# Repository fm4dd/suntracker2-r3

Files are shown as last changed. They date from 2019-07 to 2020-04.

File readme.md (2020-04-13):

# SunTracker2 Revision 3



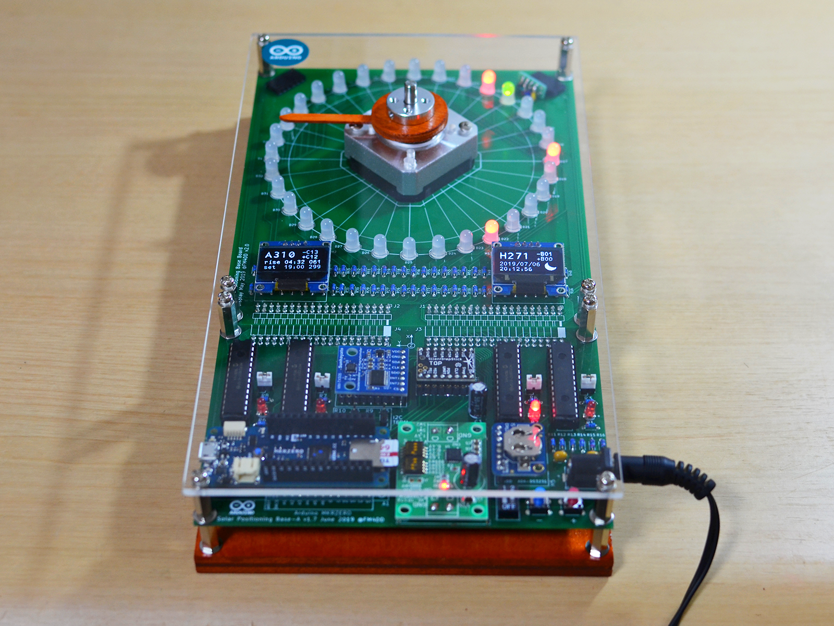
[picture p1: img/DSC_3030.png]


This project develops a photovoltaic (PV) solar tracking controller.
Pictured above is the current prototype. PV solar trackers control the PV
panel direction to keep the panel perpendicular to the Sun, maximizing the
power output. The power output difference for a fully aligned panel is
reported to be in a range of 15\~40%, which would be substantial.

## Design

The goal is a self-orienting dual-axis, scheduled, Arduino-based solar
tracker. I want to control PV panel orientation for both Elevation and
Azimuth angles (dual-axis), based on the calculated solar position of a PV
systems specific geographic location and time (scheduled).

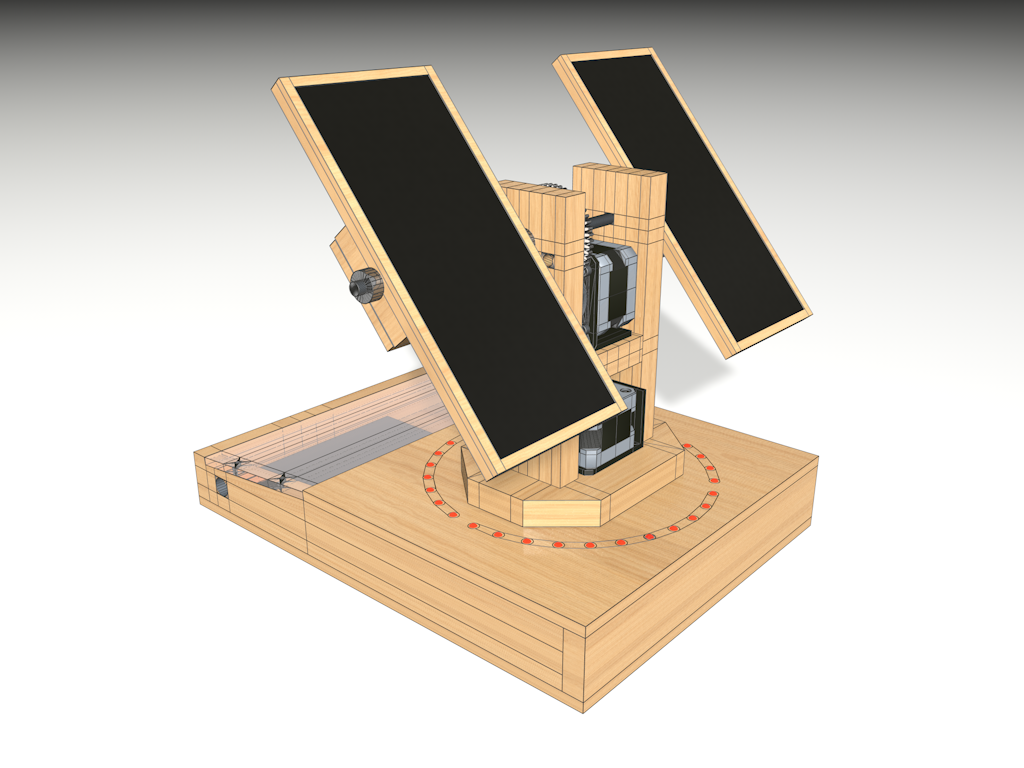
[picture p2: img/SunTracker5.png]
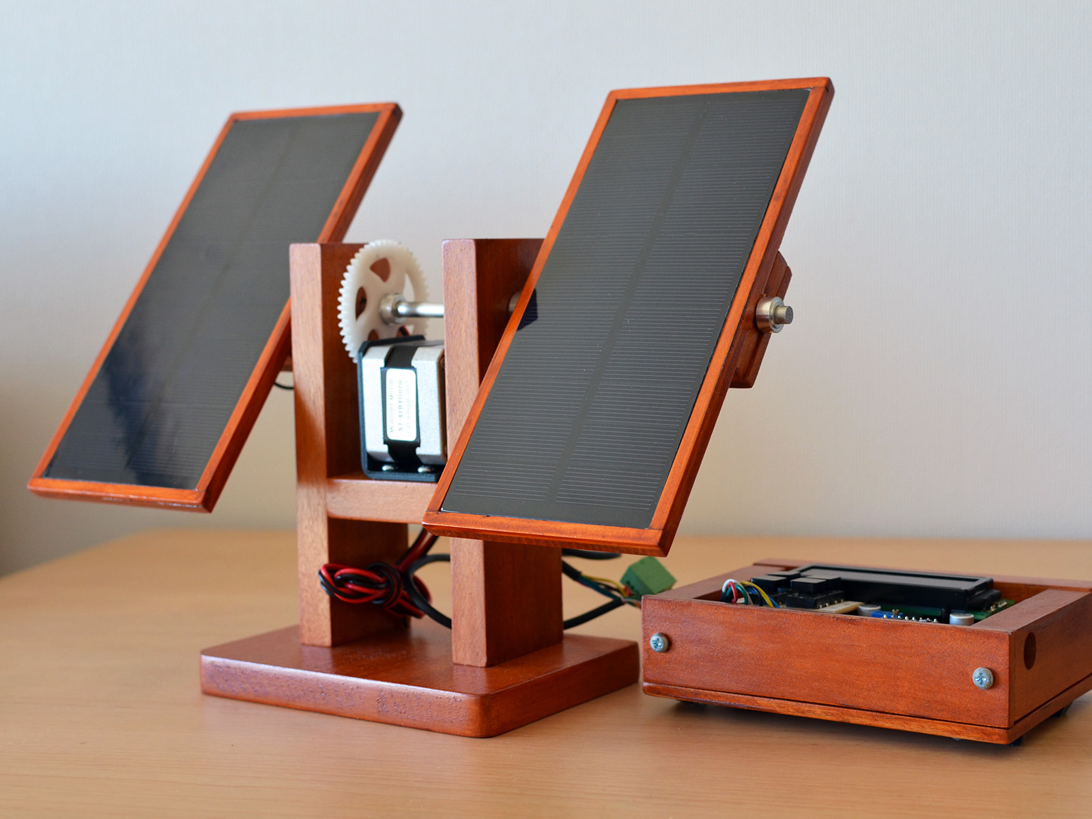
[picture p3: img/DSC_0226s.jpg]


Working under space, cost and time constraints, the prototype development is
done on a small scale model. Eventually, I want to control and optimize the
orientation of Mini-PV systems.

## Functional Design

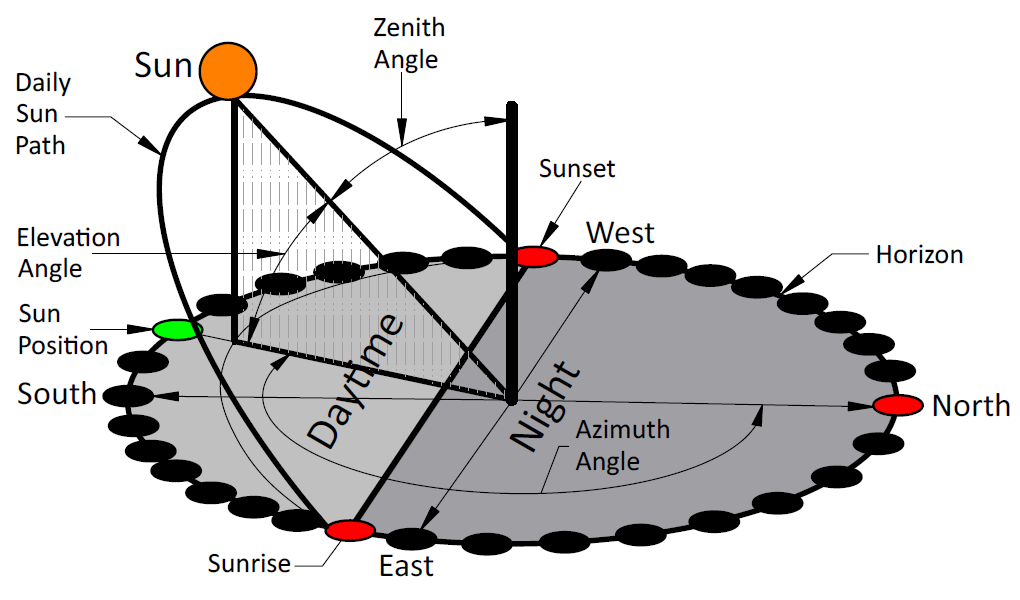
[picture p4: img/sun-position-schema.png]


In order to clearly understand and validate the sun tracking function, a 32
dual-color LED ring represents the horizon with north, sunrise and sunset
indicators. A green indicator displays the suns daily movement over time.
The optional NEMA stepper motor is used to develop the motor control code
for the solar panel horizontal alignment.

### Board Components

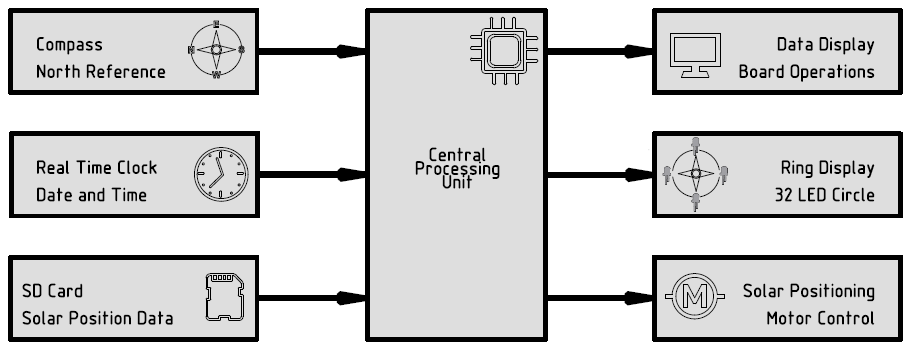
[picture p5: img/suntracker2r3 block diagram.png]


### Board Layout

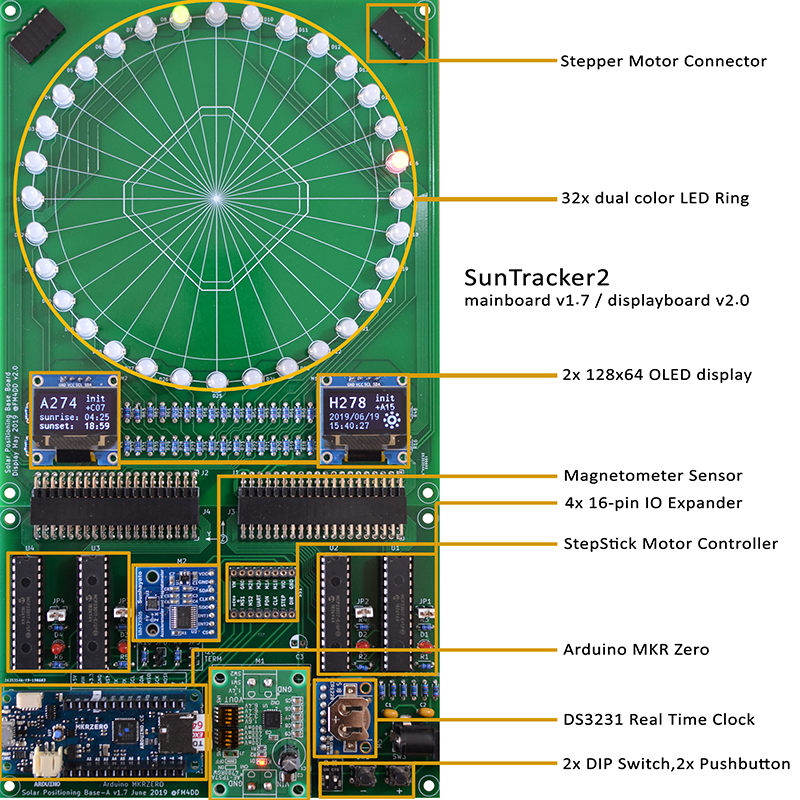
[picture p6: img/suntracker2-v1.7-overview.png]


The solar position data gets calculated off-system in advance, and saved into a
micro SD card. The pre-generated daily sun position files are then read by the
Arduino MKR Zero microcontroller through the onboard card reader. The
astronomical calculations of the suns position require sufficient CPU power, and
are taxing on Microcontrollers.

At the moment I am using a sun position dataset that covers two years of
operation, and uses approx. 20MB in size (46 MB with additional debug data). I
wrote the “suncalc” tool to pre-calculate the data set files for a specific
location, on a Linux PC.

### PCB

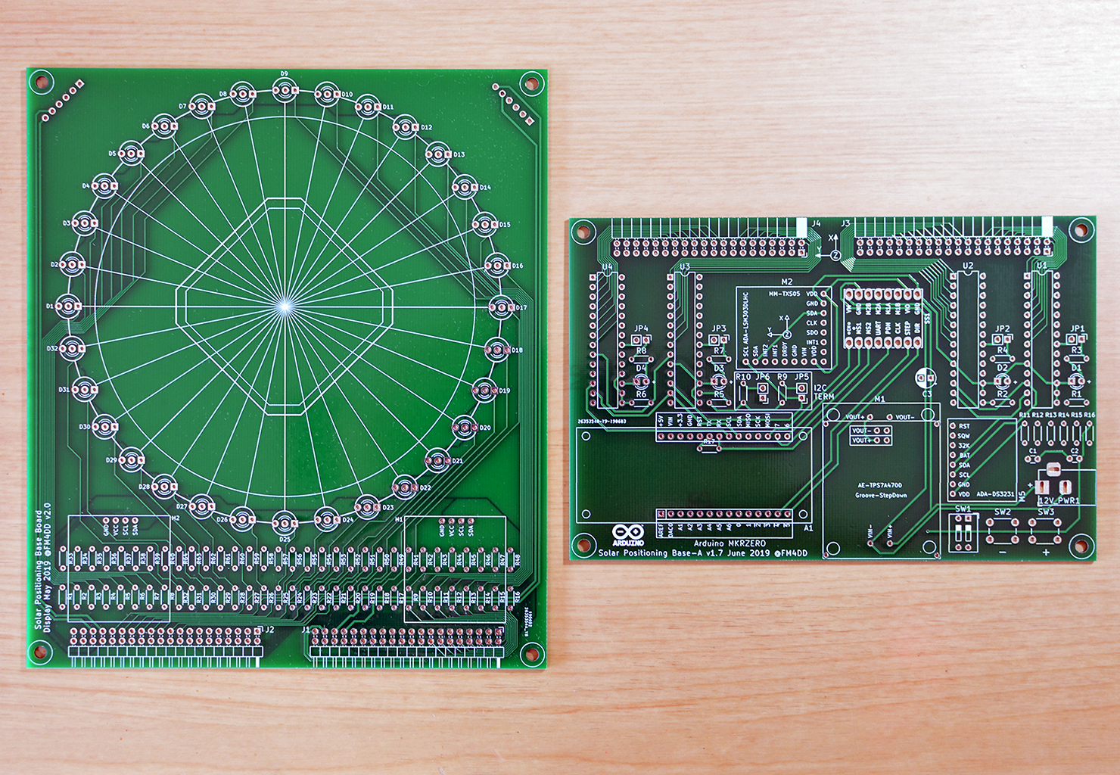
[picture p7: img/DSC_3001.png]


### Demo

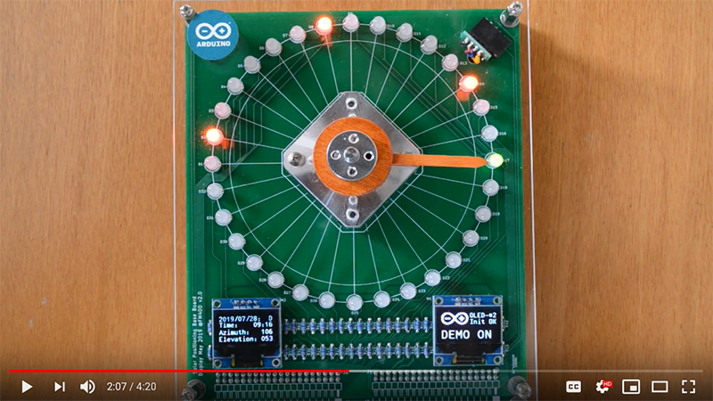
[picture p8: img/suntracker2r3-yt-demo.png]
Watch the video (https://youtu.be/e8dpviy-tlI)


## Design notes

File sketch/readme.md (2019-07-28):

# mainboard-rev3 sketch compilation

```
Sketch uses 64604 bytes (24%) of program storage space. Maximum is 262144 bytes.
Atmel SMART device 0x10010005 found
Device       : ATSAMD21G18A
Chip ID      : 10010005
Version      : v2.0 [Arduino:XYZ] Oct 20 2016 15:20:47
Address      : 8192
Pages        : 3968
Page Size    : 64 bytes
Total Size   : 248KB
Planes       : 1
Lock Regions : 16
Locked       : none
Security     : false
Boot Flash   : true
BOD          : true
BOR          : true
Arduino      : FAST_CHIP_ERASE
Arduino      : FAST_MULTI_PAGE_WRITE
Arduino      : CAN_CHECKSUM_MEMORY_BUFFER
Erase flash
done in 0.828 seconds

Write 65148 bytes to flash (1018 pages)

[=                             ] 6% (64/1018 pages)
[===                           ] 12% (128/1018 pages)
[=====                         ] 18% (192/1018 pages)
[=======                       ] 25% (256/1018 pages)
[=========                     ] 31% (320/1018 pages)
[===========                   ] 37% (384/1018 pages)
[=============                 ] 44% (448/1018 pages)
[===============               ] 50% (512/1018 pages)
[================              ] 56% (576/1018 pages)
[==================            ] 62% (640/1018 pages)
[====================          ] 69% (704/1018 pages)
[======================        ] 75% (768/1018 pages)
[========================      ] 81% (832/1018 pages)
[==========================    ] 88% (896/1018 pages)
[============================  ] 94% (960/1018 pages)
[==============================] 100% (1018/1018 pages)
done in 0.433 seconds

Verify 65148 bytes of flash with checksum.
Verify successful
done in 0.063 seconds
CPU reset.
```

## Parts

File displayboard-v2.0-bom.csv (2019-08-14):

Manufacturer Part Number | Manufacturer | Digi-Key Part Number | Customer Reference | Quantity | Description
RNMF14FTC330R | Stackpole Electronics Inc | S330CACT-ND | R1-32 | 32 | RES 330 OHM 1/4W 1% AXIAL
RNMF14FTC220R | Stackpole Electronics Inc | S220CACT-ND | R33-64 | 32 | RES 220 OHM 1/4W 1% AXIAL
PEC20DBAN | Sullins Connector Solutions | S2112E-20-ND | J1,J2 | 2 | CONN HEADER R/A 40POS 2.54MM
PPPC061LGBN-RC | Sullins Connector Solutions | S5481-ND | J3,J4 | 2 | CONN HDR 6POS 0.1 GOLD PCB R/A
ROB-09238 | SparkFun Electronics | 1568-1105-ND | M1 | 1 | STEPPER MOTOR HYBRID BIPOLAR 12V
LTL-30EHJ | Lite-On Inc. | 160-1057-ND | D1-32 | 32 | LED GRN/RED DIFFUSED T-1 3/4 T/H
SKU-0049 | SUNHOKEY Electronics Co Ltd | N/A | OLED1,OLED2 | 2 | 128X64 0.96 inch OLED Display Module SSD1306 chipset

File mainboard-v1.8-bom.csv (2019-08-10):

Manufacturer Part Number | Manufacturer | Digi-Key Part Number | Customer Reference | Quantity | Description
ABX00012 | Arduino | 1050-1137-ND | A1 | 1 | ARDUINO MKR ZERO W/ HDR ATSAMD21
MCP23017-E/SP | Microchip Technology | MCP23017-E/SP-ND | U1,U2,U3,U4 | 4 | IC I/O EXPANDER I2C 16B 28SDIP
ED281DT | On Shore Technology Inc. | ED3050-5-ND | SU1, SU2, SU3, SU4 | 4 | CONN IC DIP SOCKET 28POS TIN
1120 | Adafruit Industries LLC | 1528-1173-ND | M2 | 1 | BOARD ACCEL/COMPASS 3AXIS LSM303
3013 | Adafruit Industries LLC | 1528-1598-ND | M5 | 1 | ADAFRUIT DS3231 PRECISION RTC BR
TMC2208 SILENTSTEPSTICK | Trinamic Motion Control GmbH | 1460-1201-ND | SS1 | 1 | TMC2208 STEPPER DRIVER BOARD
1825057-1 | TE Connectivity ALCOSWITCH Switches | 450-1363-ND | SWI1 | 1 | SWITCH SLIDE DIP SPST 100MA 24V
151031SS04000 | Wurth Electronics Inc. | 732-5005-ND | D1,D2,D3,D4 | 4 | LED RED DIFFUSED 3MM ROUND T/H
C320C105K5N5TA91707301 | KEMET | 399-14394-1-ND | C1,C2 | 2 | CAP CER 1UF 50V X8L RADIAL
68786-102LF | Amphenol ICC (FCI) | 609-3121-ND | JP1,JP2,JP3,JP4,JP5,JP6 | 6 | CONN SHUNT 2POS .100 LOPRO GOLD
476CKE035M | Illinois Capacitor | 1572-1473-ND | C3 | 1 | CAP ALUM 47UF 20% 35V RADIAL
PPTC202LJBN-RC | Sullins Connector Solutions | S5534-ND | J3,J4 | 2 | CONN HDR 40POS 0.1 TIN PCB R/A
SMC-1-40-1-GT | Adam Tech | 2057-SMC-1-40-1-GT-ND | Circuit Sockets | 2 | MACHINE PIN SOCKET 40P 1.00MM PI
1825910-6 | TE Connectivity ALCOSWITCH Switches | 450-1650-ND | SWI2,SWI3 | 2 | SWITCH TACTILE SPST-NO 0.05A 24V
RNMF14FTC10K0 | Stackpole Electronics Inc | S10KCACT-ND | R1,R2,R5,R6,R9,R10,R11,R12,R13,R14 | 10 | RES 10K OHM 1/4W 1% AXIAL
RNMF14FTC330R | Stackpole Electronics Inc | S330CACT-ND | R3,R4,R7,R8 | 4 | RES 330 OHM 1/4W 1% AXIAL
RNMF14FTC2K20 | Stackpole Electronics Inc | S2.2KCACT-ND | R15,R16 | 2 | RES 2.2K OHM 1/4W 1% AXIAL
PJ-002A | CUI Inc. | CP-002A-ND | 12V Barrel Jack | 1 | CONN PWR JACK 2X5.5MM SOLDER

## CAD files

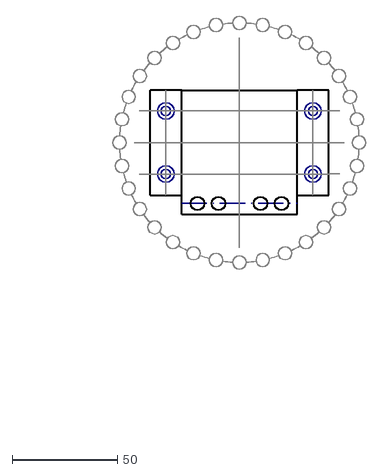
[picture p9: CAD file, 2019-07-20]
cad/32LED ring -114cm with Stand.dxf
166.4 x 198.3

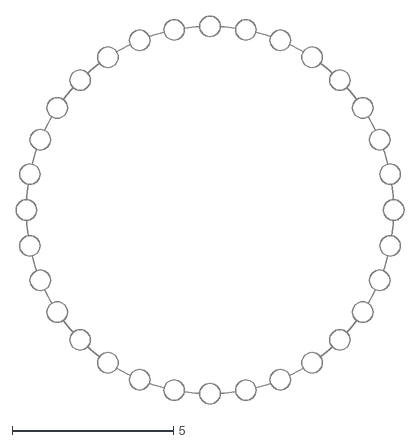
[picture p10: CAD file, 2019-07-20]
cad/32LED ring -114cm.dxf
12.0 x 12.0

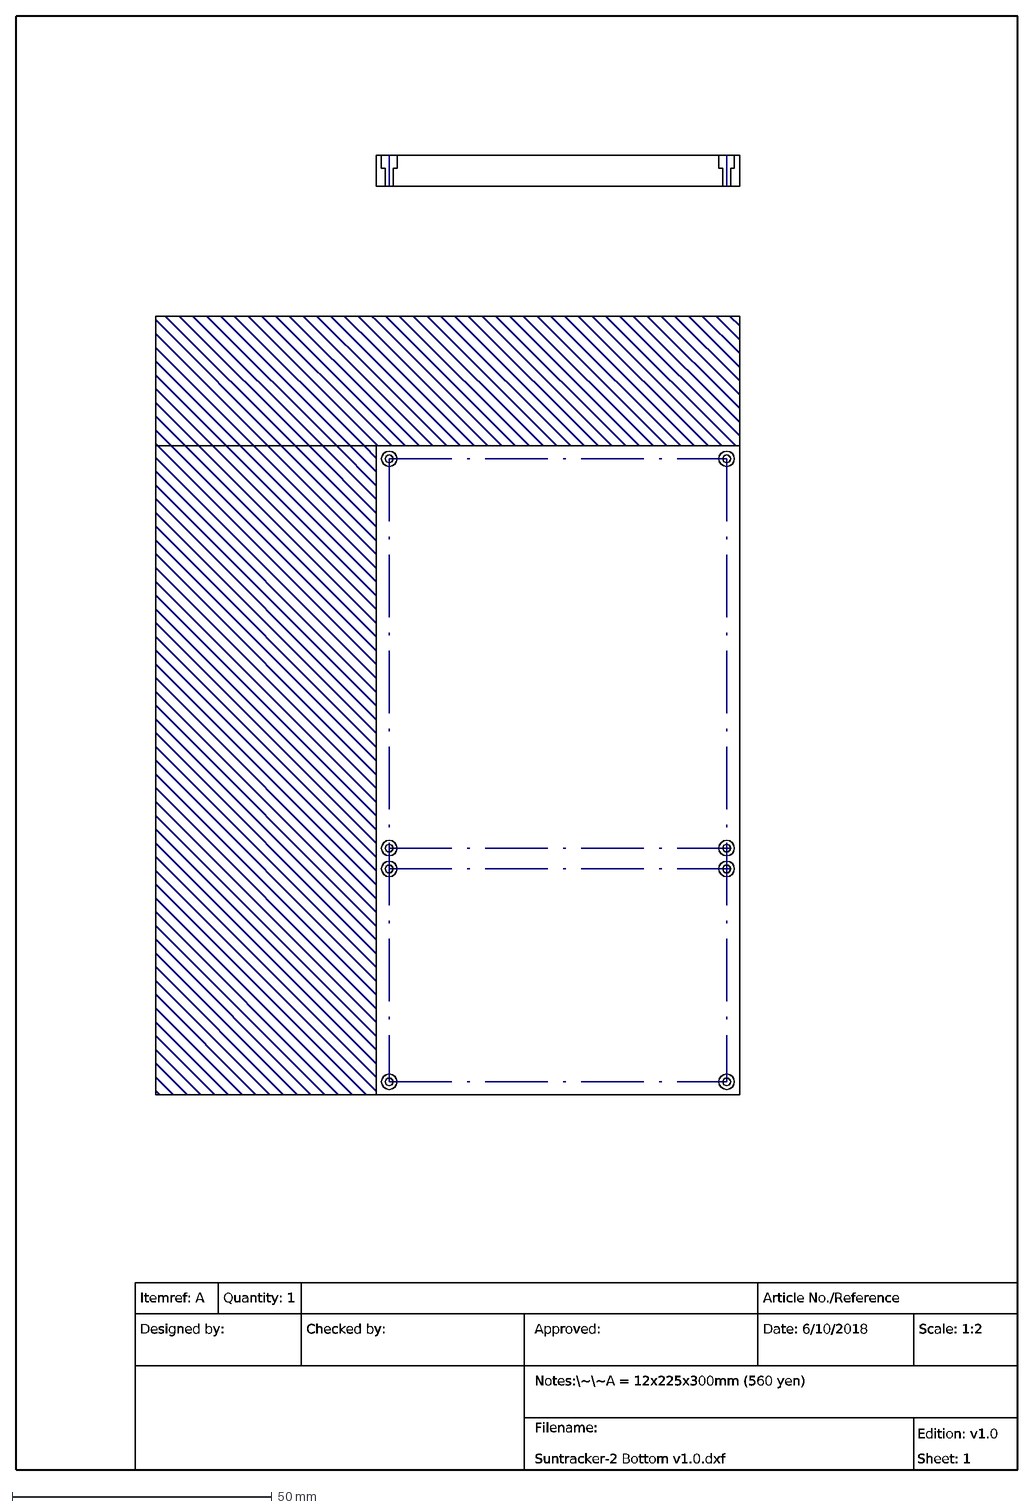
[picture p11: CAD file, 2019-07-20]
cad/20190620 Suntracker2 Bottom v1.0.dxf
Notes:\~\~A = 12x225x300mm (560 yen)
Itemref: A
Quantity: 1
Article No./Reference
Designed by:
Checked by:
Approved:
Filename: Suntracker-2 Bottom v1.0.dxf
Date: 6/10/2018
Scale: 1:2
Edition: v1.0 Sheet: 1

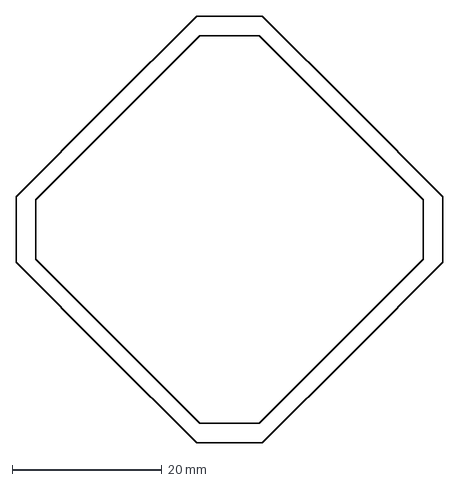
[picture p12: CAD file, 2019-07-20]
cad/20190601 stepper motor footprint.dxf
57.0 x 57.0 mm

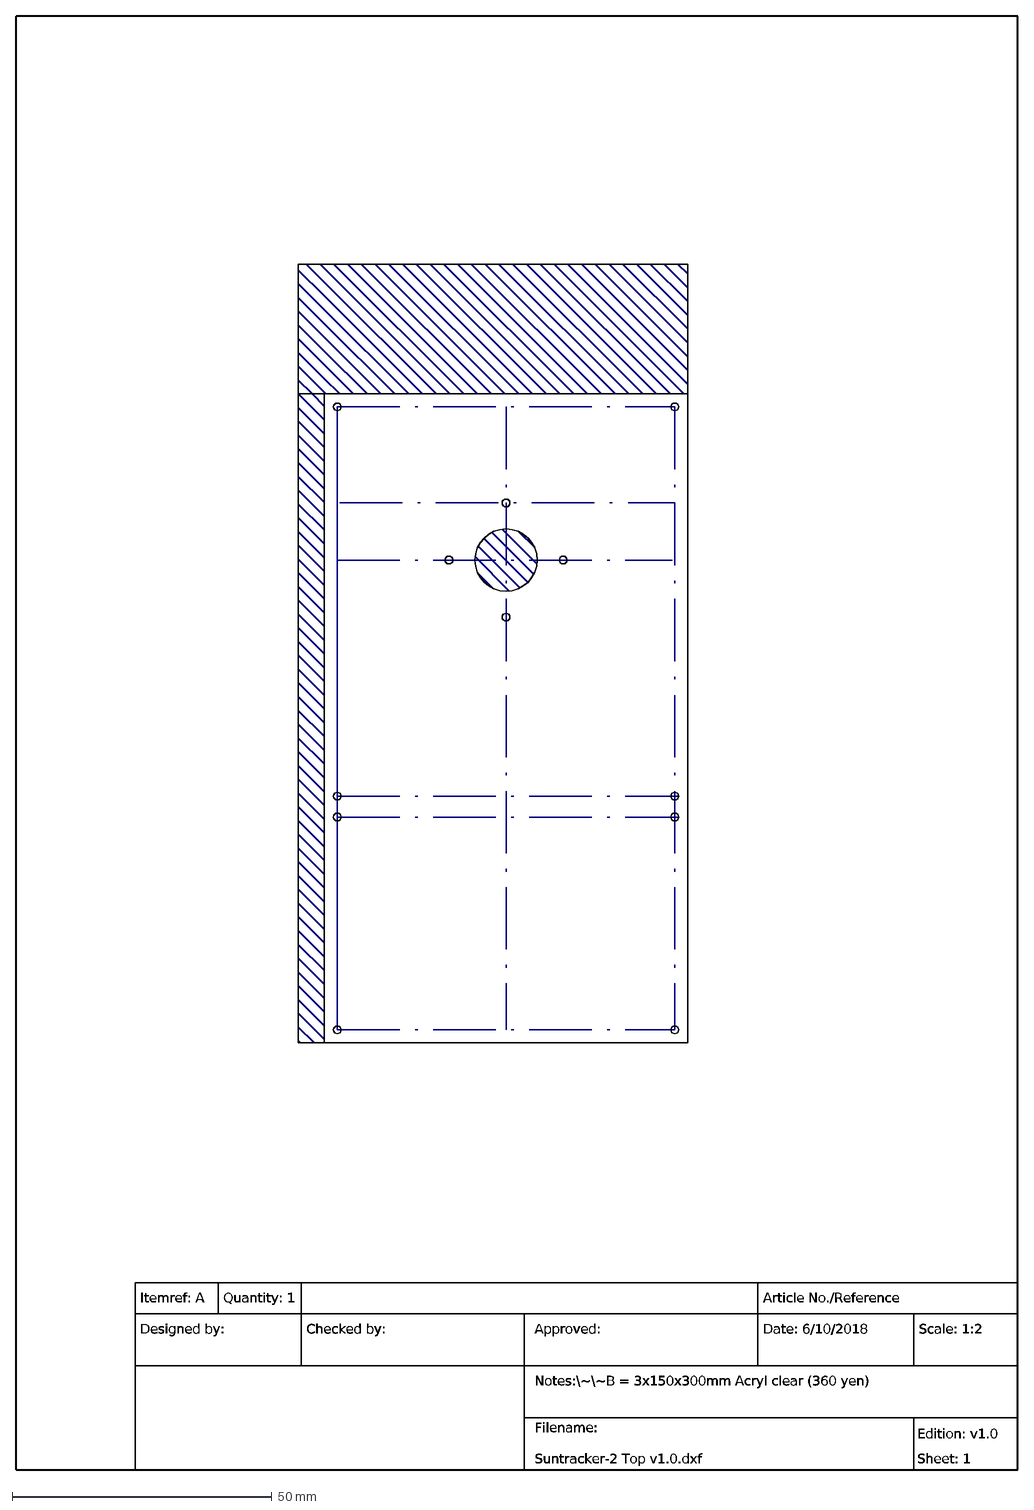
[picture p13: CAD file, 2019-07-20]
cad/20190620 Suntracker2 Top v1.0.dxf
Notes:\~\~B = 3x150x300mm Acryl clear (360 yen)
Itemref: A
Quantity: 1
Article No./Reference
Designed by:
Checked by:
Approved:
Filename: Suntracker-2 Top v1.0.dxf
Date: 6/10/2018
Scale: 1:2
Edition: v1.0 Sheet: 1

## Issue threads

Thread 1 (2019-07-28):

OLED display-1 I2C wire flip between control board v1.7 and displayboard v2.0

fm4dd, 2019-07-28:
A wire re-routing oversight during PCB design introduced a I2C connection wire flip for the OLED-1 I2C bus, on the boards interconnect.

Details:

mainboard v1.7, connector J4: SCL --> pin36, SDA --> pin 38
displayboard v2.0, connector J2: SDA --> pin 36, SCL --> pin 38

One of the boards design needs to get updated after identifying the best place to make the routing change. Its most likely that mainboard v1.7 gets updated to v1.8, with new Gerber files to be published. I am currently running a wire bridge to compensate.

fm4dd, 2019-08-04:
The mainboard has been revised and updated to v1.8. The new gerber files have been added to fix this issue.

Closed 2019-08-04.

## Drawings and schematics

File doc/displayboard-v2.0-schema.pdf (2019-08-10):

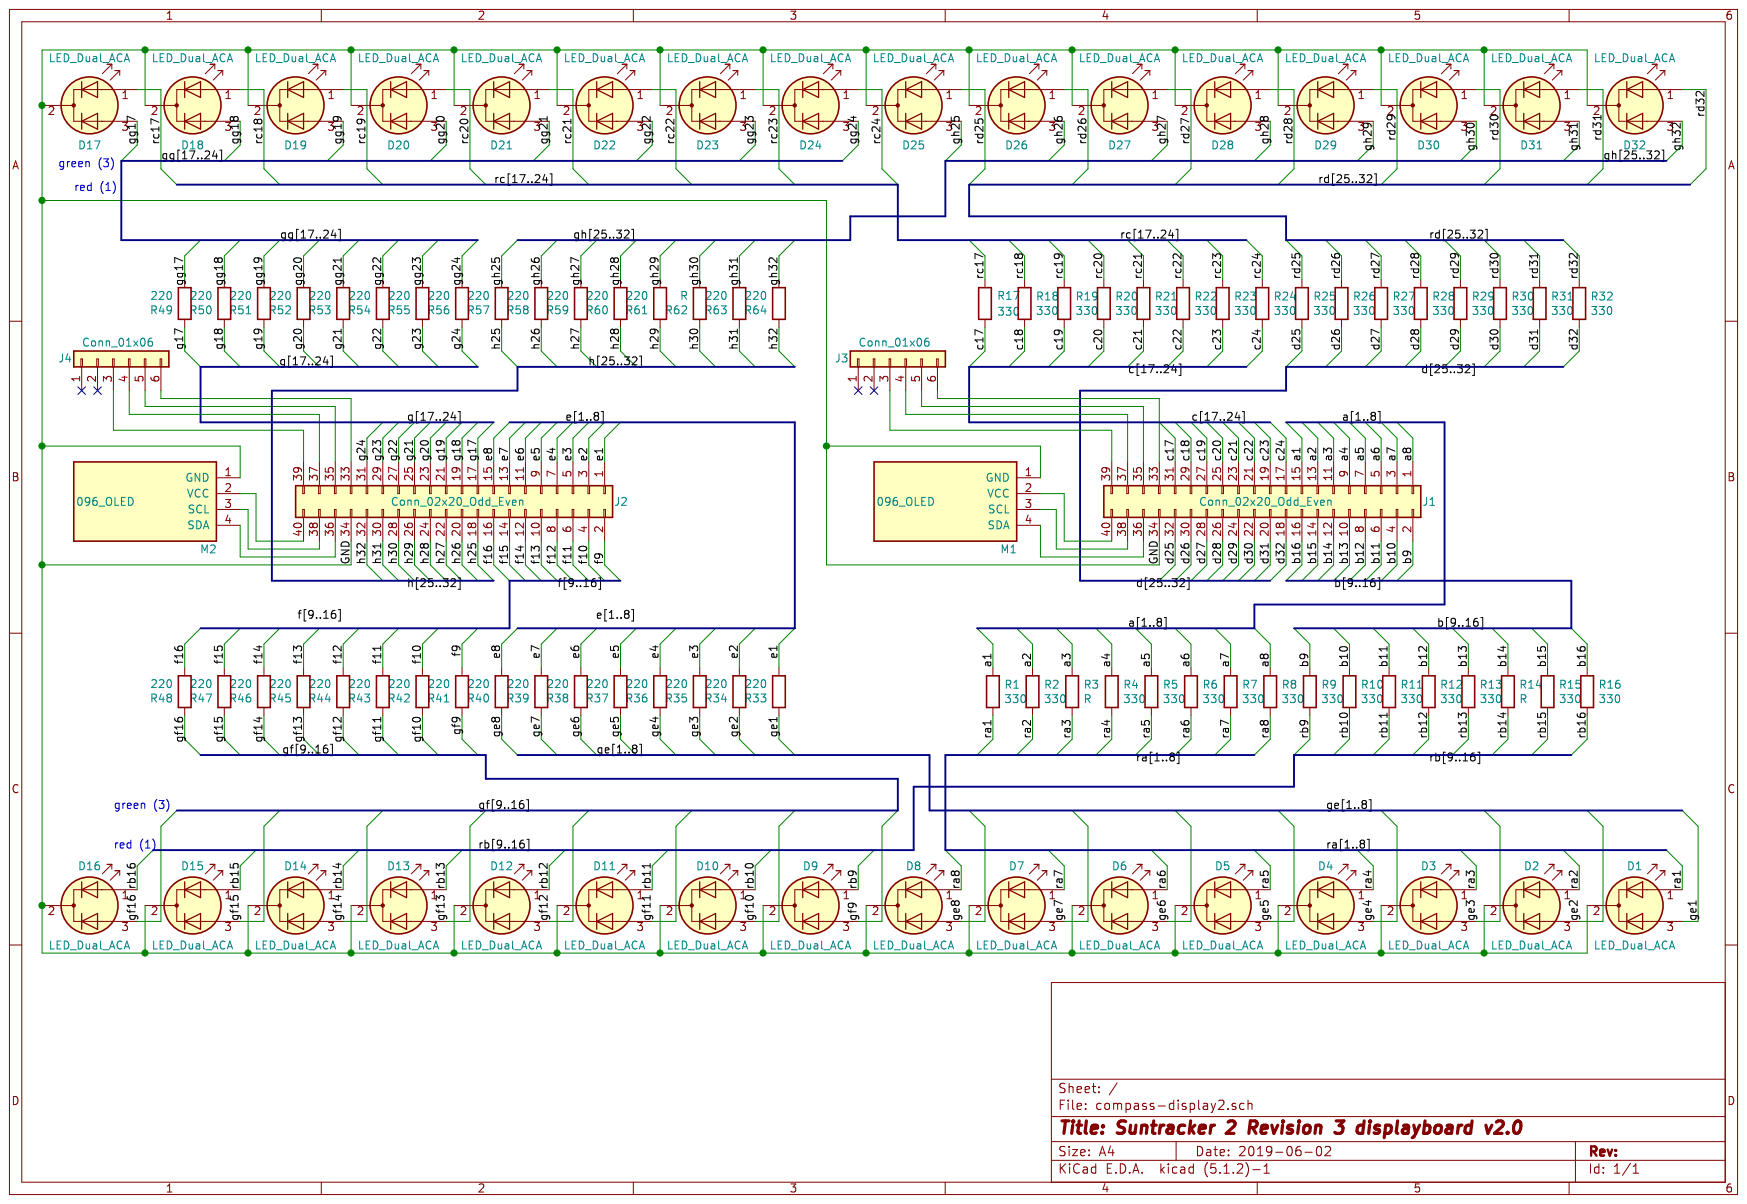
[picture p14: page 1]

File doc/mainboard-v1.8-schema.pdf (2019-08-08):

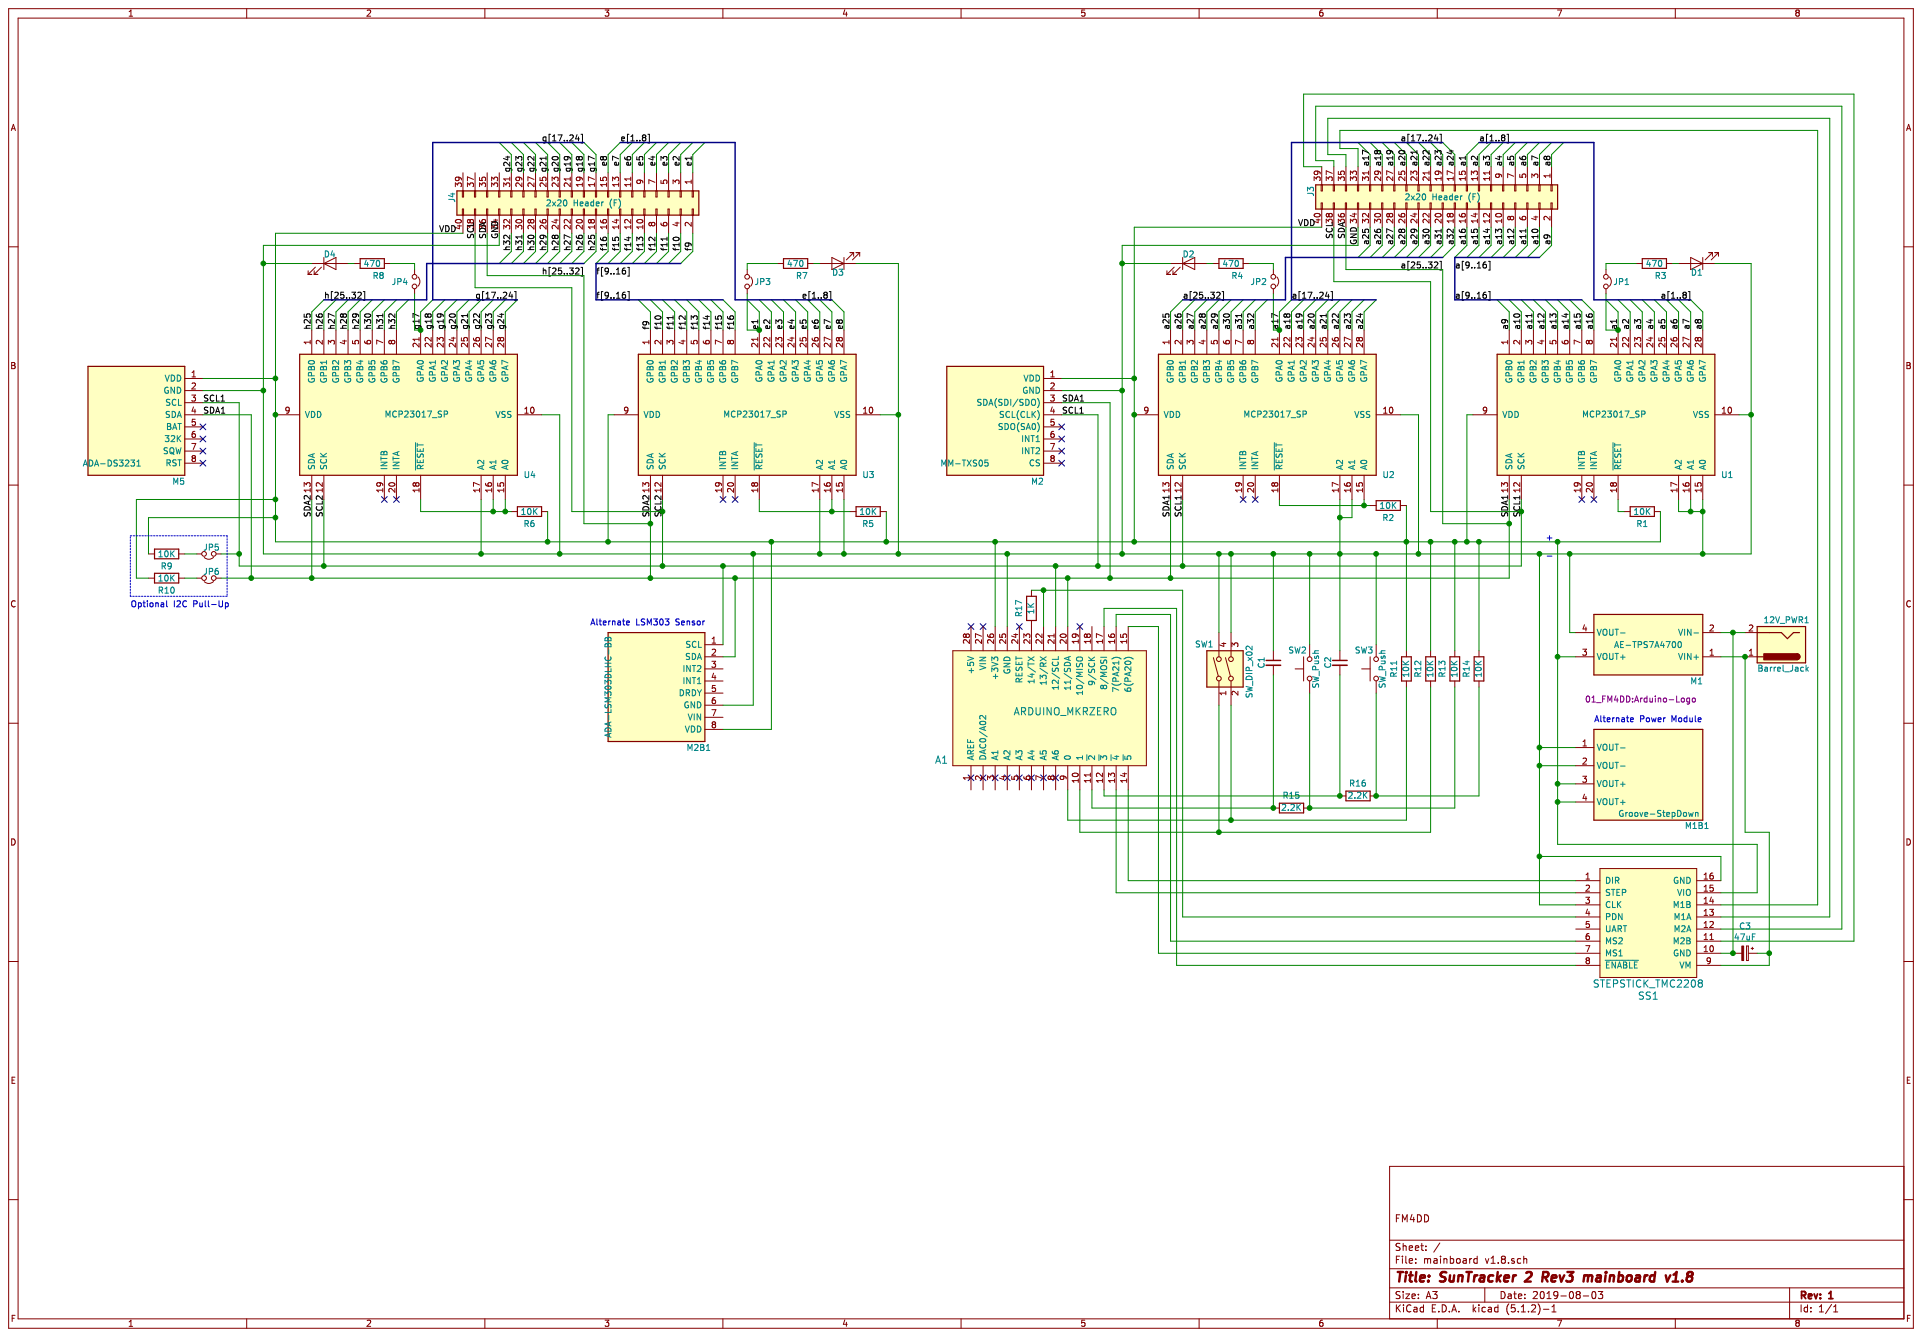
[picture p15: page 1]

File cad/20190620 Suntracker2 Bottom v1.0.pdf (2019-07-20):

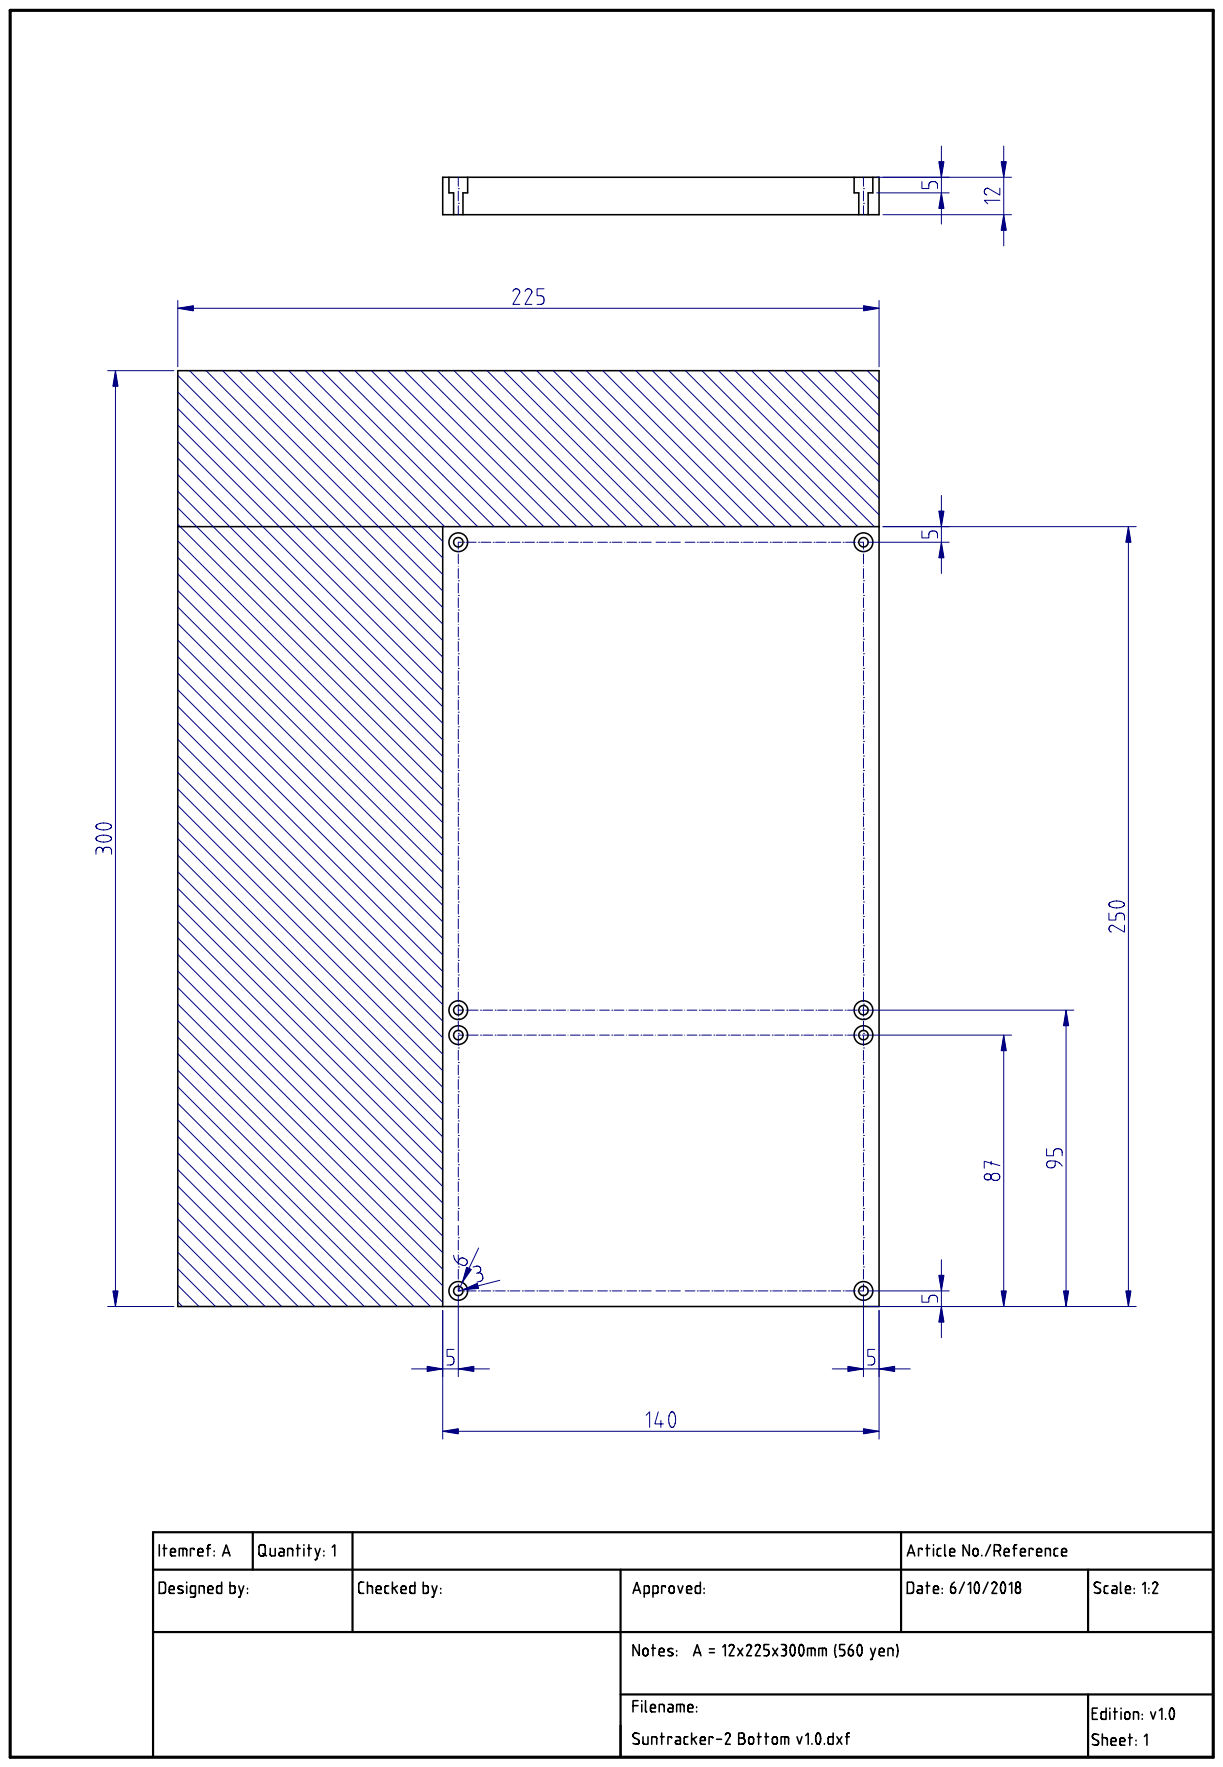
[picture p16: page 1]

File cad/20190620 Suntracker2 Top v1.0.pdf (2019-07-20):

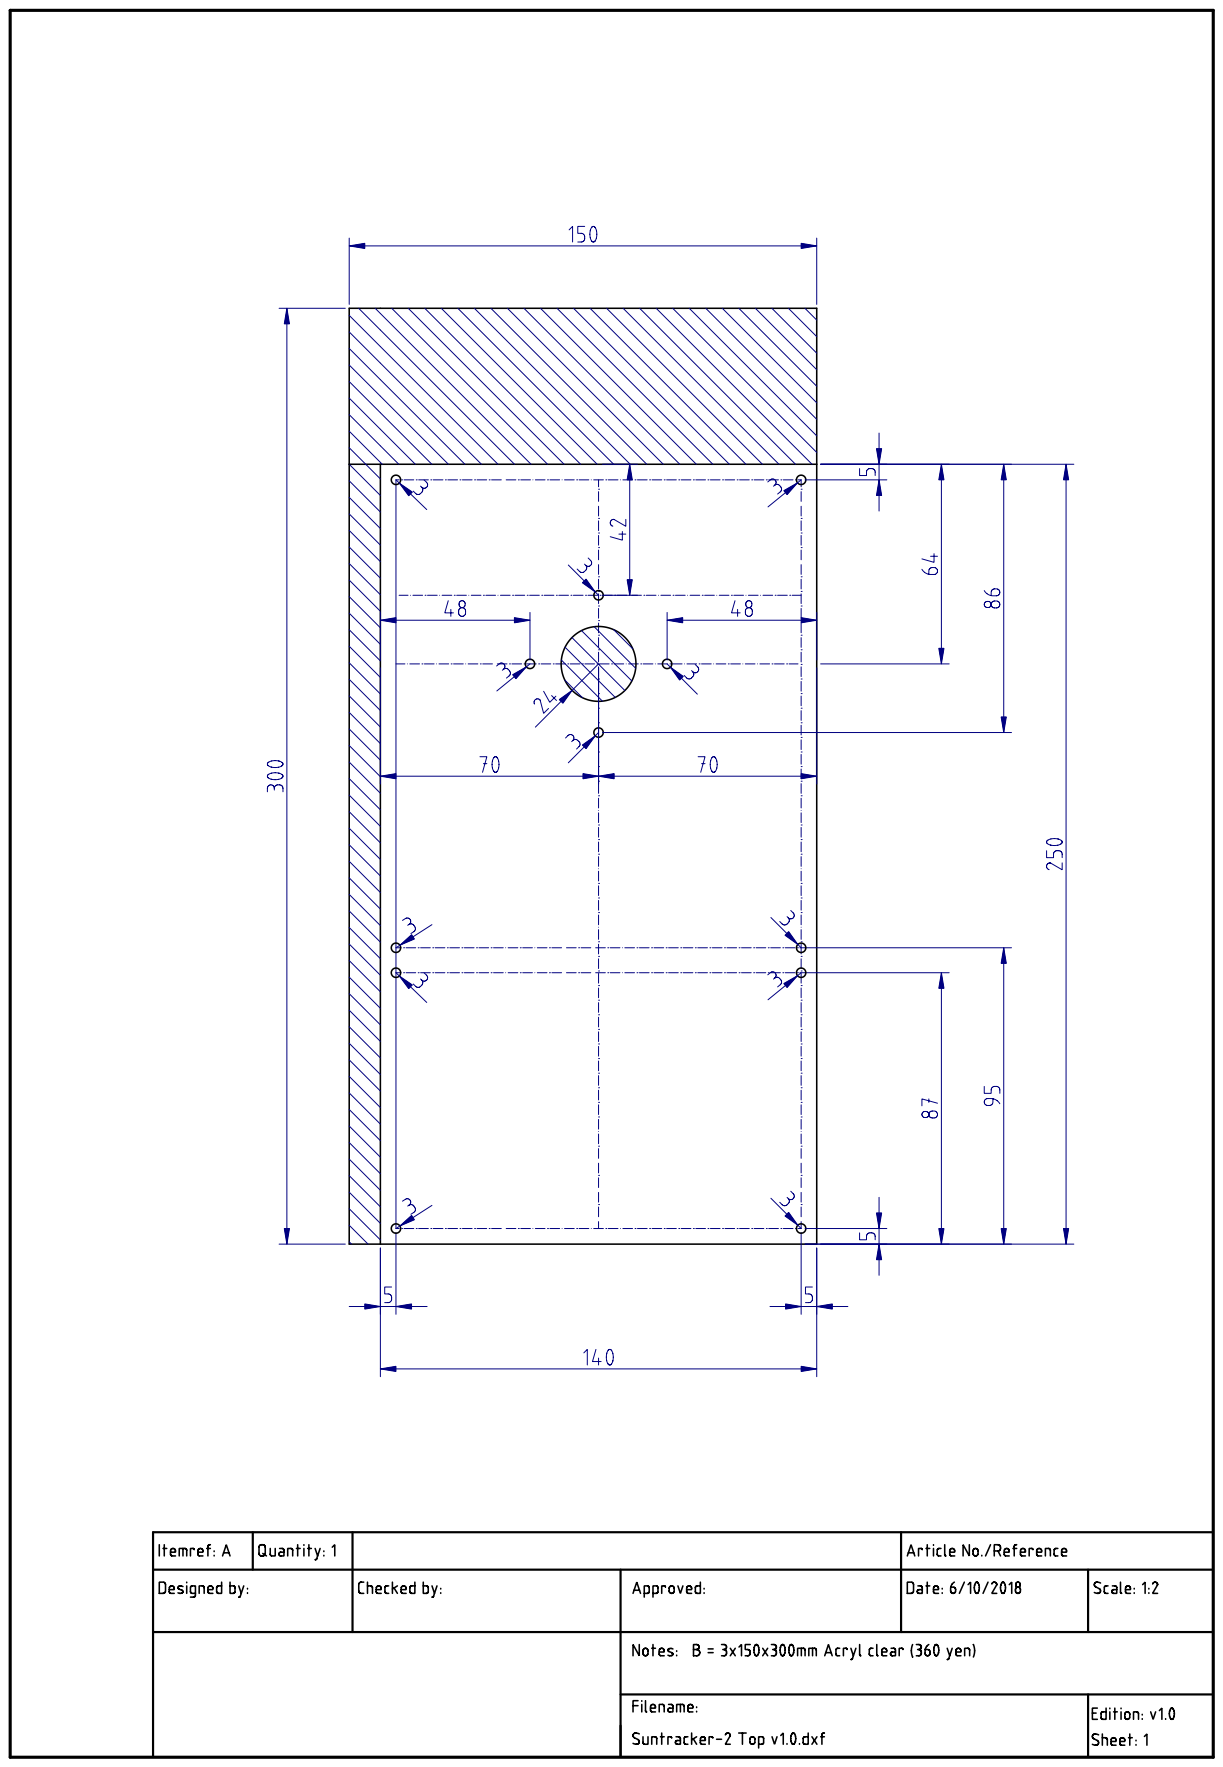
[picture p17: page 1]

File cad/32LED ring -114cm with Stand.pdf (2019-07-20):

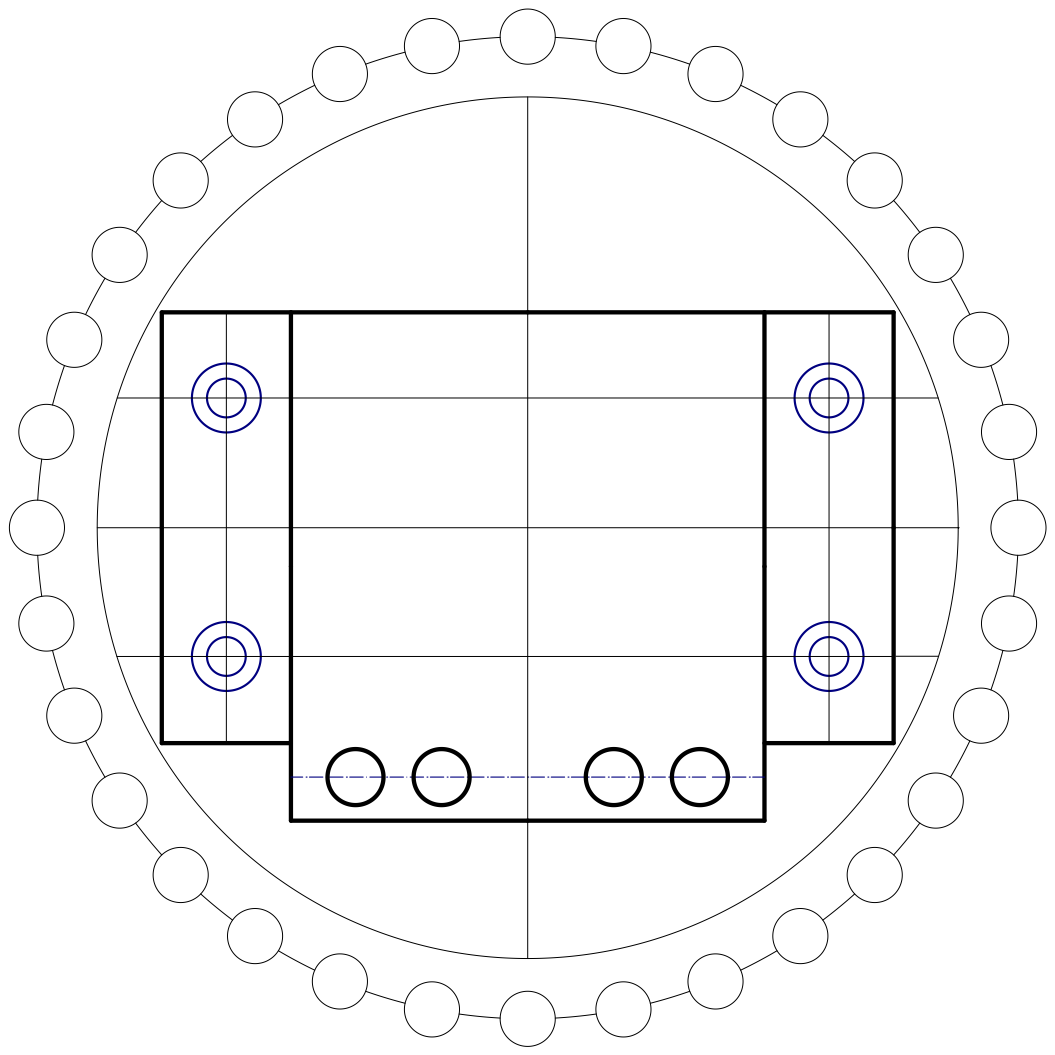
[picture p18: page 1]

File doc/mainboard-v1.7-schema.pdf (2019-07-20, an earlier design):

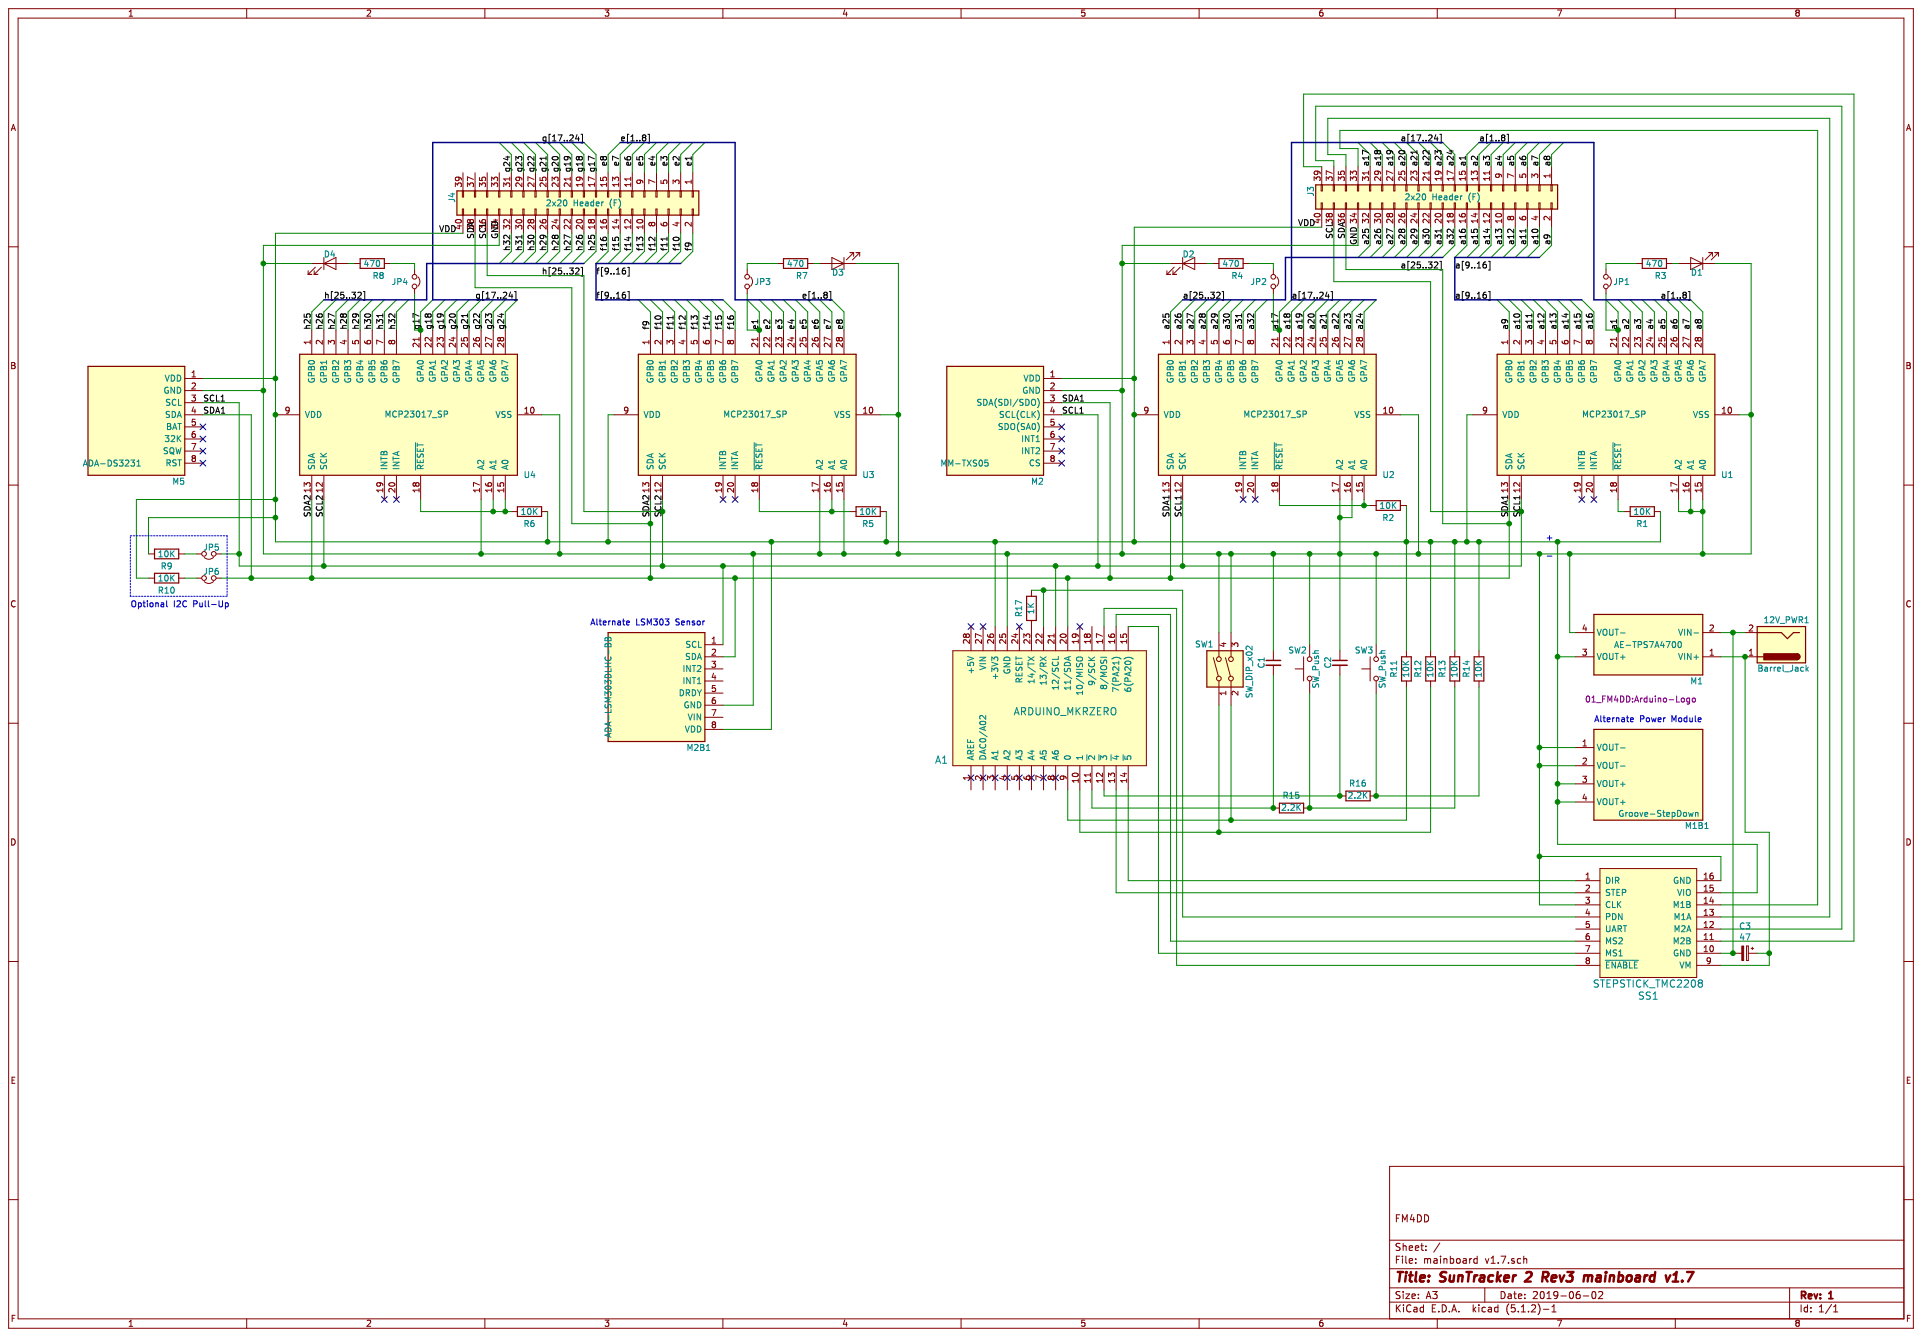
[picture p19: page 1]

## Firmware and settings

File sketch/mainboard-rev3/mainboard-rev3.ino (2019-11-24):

/* ------------------------------------------------- *
 * Suntracker2  mainboard-rev3  June 2019 @ FM4DD    *
 *                                                   * 
 * This code controls Suntracker2 Base-Board v1.7 w. *
 * Displayboard v2.0 for solar azimuth path tracking *
 * Requires suncalc v1.2 generated solar positioning *
 * dataset stored in the root of the MKRZERO MicroSD *
 * ------------------------------------------------- */
#include <Wire.h>              // Arduino default 12C libary
#include <Arduino.h>           // Arduino default library
#include <SPI.h>               // Arduino default SPI library
#include <SD.h>                // Arduino default SD library
#include "LSM303.h"            // https://github.com/pololu/lsm303-arduino
/* ------------------------------------------------- *
 * The U8g2 lib has been modified for dual-1306 Oled *
 * and was placed into the sketch folder under src.  *
 * Its stripped down to a single SSD1306 device type *
 * The lib is 28MB, due to a 25MB u8g2_fonts.c file. *
 * ------------------------------------------------- */
#include "src/U8g2lib.h"       // https://github.com/olikraus/u8g2
#include "uRTCLib.h"           // https://github.com/Naguissa/uRTCLib
#include "ledring.h"           // local code module for the 32 LED ring
#include "oledimg.h"           // bitmap files for the two OLED displays

/* ------------------------------------------------- */
/* DEBUG enables debug output to the serial monitor  */
/* ------------------------------------------------- */
//#define DEBUG

/* ------------------------------------------------- */
/* SLOW and FAST set motor speed if stepper is used  */
/* ------------------------------------------------- */
#define SLOW 5000
#define FAST 500

/* ------------------------------------------------- */
/* SD card - Arduino MKRZero onboard card reader     */
/* ------------------------------------------------- */
Sd2Card card;
SdVolume volume;
SdFile root;
const int chipSelect = SDCARD_SS_PIN;
/* ------------------------------------------------- */
/* Magnetic field Sensor                             */
/* ------------------------------------------------- */
LSM303 compass;
/* ------------------------------------------------- */
/* 2x Oled Display - U8G2_R0 = orientation normal    */
/* ------------------------------------------------- */
U8G2_SSD1306_128X64_NONAME_F_HW_I2C oled1(U8G2_R0);
U8G2_SSD1306_128X64_NONAME_F_HW_I2C_2 oled2(U8G2_R0);

/* ------------------------------------------------- */
/* DS3231 Precision RTC clock                        */
/* ------------------------------------------------- */
uRTCLib rtc;

/* ------------------------------------------------- */
/* DisplayBoard LedRing initializer                  */
/* ------------------------------------------------- */
ledRing ring;

/* ---------------------------------------------------- */
/* 4x IO Expanders for a total of 64 I/O ports          */
/* ---------------------------------------------------- */
extern Adafruit_MCP23017 mcp1;
extern Adafruit_MCP23017 mcp2;
extern Adafruit_MCP23017 mcp3;
extern Adafruit_MCP23017 mcp4;

/* ------------------------------------------------- */
/* Global variable list                              */
/* ------------------------------------------------- */
int8_t hled = 0;             // heading LED (red)
int8_t oldhled = 33;         // 33 > max value 32, indicates "init"
int8_t aled = 0;             // azimuth LED (green)
int8_t oldaled = 33;         // 33 > max value 32, indicates "init"
int8_t rled = 0;             // sunrise LED (red)
int8_t oldrled = 33;         // 33 > max value 32, indicates "init"
int8_t sled = 0;             // sunset LED (red)
int8_t oldsled = 33;         // 33 > max value 32, indicates "init"
uint8_t risehour = 0;        // hour of sunrise
uint8_t risemin = 0;         // minute of sunrise
uint8_t transithour = 0;     // peak altitude hour
uint8_t transitmin = 0;      // peak altitude minute
uint8_t sethour = 0;         // sunset hour
uint8_t setmin = 0;          // sunset minute
float heading;               // North heading
int16_t hdg;                 // North heading, rounded to 0..360
double azimuth;              // sun azimuth angle, north->eastward
double zenith;               // zenith angle, substract from 90 to get altitude
uint16_t riseaz;             // sunrise azimuth, rounded to full degrees
int16_t transalt;            // transit altitude - solar noon peak altitude
uint16_t setaz;              // sunset azimuth, rounded to full degrees
boolean daylight;            // daylight flag, false = night
char lineStr[15];            // display output buffer, 14-chars + \0
char hledStr[5];             // display LED control "-B01"
char dirStr[6];              // display north angle "H263"
char aziStr[6];              // display azimuth angle "A134"
char timeStr[9];             // display time string "HH:MM:SS"
char dateStr[16];            // display date string "YYYY/MM/DD"
char riseStr[16];            // display string "sunrise: 06:45"
char setStr[16];             // display string "sunset:  18:10"
char binfile[13];            // daily sun data file yyyymmdd.bin
char srsfile[13];            // sunrise/sunset file srs-yyyy.bin
const uint8_t dip1  = 0;     // GPIO pin dipswitch-1 on GPIO-0
const uint8_t dip2  = 1;     // GPIO pin dipswitch-2 on GPIO-1
const uint8_t push1 = 2;     // GPIO pin pushbutton-1 on GPIO-2
const uint8_t push2 = 3;     // GPIO pin pushbutton-2 on GPIO-3
const uint8_t step1 = 4;     // GPIO pin stepper motor-1 step
const uint8_t dir1  = 5;     // GPIO pin stepper motor-1 direction
const uint8_t ms11  = 6;     // GPIO pin stepper motor-1 step size 1
const uint8_t ms21  = 7;     // GPIO pin stepper motor-1 step size 2
const uint8_t ena1  = 8;     // GPIO pin stepper motor-1 enable
const double mdecl = -7.583; // local magnetic declination
uint8_t dippos1 = 0;         // dipswitch 1 position (extra tests)
uint8_t dippos2 = 0;         // dipswitch 2 position (motor enable)
uint16_t m1cpos = 0;         // stepper motor-1 current step position (0..1599)
uint16_t m1tpos = 0;         // stepper motor-1 target step position (0..1599)
boolean m1move = false;      // stepper motor-1 "move in progress" flag
uint8_t opmode = 0;          // operations mode: 0 = normal, 1 = demo
uint16_t day_azi[1440];      // daily azimuth angle 0..360, 1min interval, 2.88KB
int16_t day_ele[1440];       // daily elevation angle -90 ..90, 1min interval 2.88KB

void setup() {
#ifdef DEBUG
  /* ------------------------------------------------- */
  /* Enable Serial Debug output                        */
  /* ------------------------------------------------- */
  Serial.begin(9600);
  while (!Serial);   // wait for serial port to connect.
  Serial.println("Serial Debug Start");
#endif
  /* ------------------------------------------------- */
  /* Set dipswitch GPIO ports as input                 */
  /* ------------------------------------------------- */
  pinMode(dip1, INPUT);
  pinMode(dip2, INPUT);
  dippos1 = digitalRead(dip1);
  dippos2 = digitalRead(dip2);    
  /* ------------------------------------------------- */
  /* Set pushbutton GPIO ports as input                */
  /* ------------------------------------------------- */
  pinMode(push1, INPUT);
  pinMode(push2, INPUT);
  /* ------------------------------------------------- */
  /* Pushbutton 1 (-) at startup triggers demo LOW=ON  */
  /* demo mode switches main loop from min to sec exec */
  /* ------------------------------------------------- */
  if(digitalRead(push1) == LOW) opmode = 1; // demo mode
  /* ------------------------------------------------- */
  /* Set motor-1 control pins as output                */
  /* ------------------------------------------------- */
  pinMode(step1,OUTPUT); 
  pinMode(dir1,OUTPUT);
  pinMode(ena1,OUTPUT);
  pinMode(ms11,OUTPUT);
  pinMode(ms21,OUTPUT);
  digitalWrite(ena1,HIGH); // Disable stepstick1
  /* ------------------------------------------------- */
  /* Enable I2C bus                                    */
  /* ------------------------------------------------- */
  Wire.begin();
  /* ------------------------------------------------- */
  /* Enable the OLED graphics display 14char line font */
  /* ------------------------------------------------- */
  oled1.setI2CAddress(0x3C * 2);
  oled2.setI2CAddress(0x3D * 2);
  oled1.begin();
  oled2.begin();
  oled1.setFont(u8g2_font_t0_17_mr);
  oled2.setFont(u8g2_font_t0_17_mr);
  oled1.setFontMode(0);
  oled2.setFontMode(0);
  
  oled1.drawXBMP(0,0, 64, 32, arduLogo);
  oled1.drawStr(67, 14, "MKRZERO");
  oled1.drawStr(67, 29, "Init OK");
  oled1.sendBuffer();

  oled2.drawXBMP(0,0, 64, 32, arduLogo);
  oled2.drawStr(67, 14, "OLED-#2");
  oled2.drawStr(67, 29, "Init OK");
  snprintf(lineStr, sizeof(lineStr), "2xOLED display");
  oled2.drawStr(0, 47, lineStr);
  snprintf(lineStr, sizeof(lineStr), "enabled");
  oled2.drawStr(0, 63, lineStr);
  oled2.sendBuffer();
  delay(2000);
  /* ------------------------------------------------- */
  /* 1st dip switch enables extended selftests, LOW=ON */
  /* ------------------------------------------------- */
  if(dippos1 == LOW) {
    oled1.drawStr(67, 14, "Modules");
    oled1.drawStr(67, 29, "Testrun");
    /* ------------------------------------------------- */
    /* Identify I2C devices                              */
    /* 0x1D = MM-TXS05 (LSM303D)                         */
    /* 0x20, 0x21, 0x22, 0x23 = MCP23017 1-4             */
    /* 0x3C, 0x3D = SD1306 OLED                          */
    /* 0x68 = DS3231 RTC                                 */
    /* ------------------------------------------------- */
    const int size = 8;
    byte addr[8] = { 0x1D, 0x20, 0x21, 0x22, 0x23, 0x3C, 0x3D, 0x68 };
    int i;
    byte error;
    for(i = 0; i<size; i++ ) {
      /* ------------------------------------------------- */
      /* The i2c_scanner uses the Write.endTransmisstion   */
      /* return value to see if device exists at the addr  */
      /* ------------------------------------------------- */
      snprintf(lineStr, sizeof(lineStr), "I2C check %02x  ", addr[i]);
      oled1.drawStr(0, 47, lineStr);
      oled1.sendBuffer();
      Wire.beginTransmission(addr[i]);
      error = Wire.endTransmission();
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
void loop() {
  /* ------------------------------------------------- */
  /* Aquire time                                       */
  /* Every new minute read solar position data         */
  /* ------------------------------------------------- */
  rtc.refresh();
  if(rtc.second() == 0) {
    if(rtc.minute() == 0) {
      snprintf(binfile, sizeof(binfile), "20%d%02d%02d.BIN", 
                rtc.year(),rtc.month(),rtc.day());
      if(rtc.day() == 1) {
        snprintf(srsfile, sizeof(srsfile), "SRS-20%d.BIN", 
                rtc.year());
      }
      get_suntime(srsfile);
      snprintf(riseStr, sizeof(riseStr), "rise %02d:%02d %03d",
               risehour,risemin, riseaz);
      snprintf(setStr, sizeof(setStr), "set  %02d:%02d %03d",
               sethour, setmin, setaz);
    }
    solar_position(binfile);
    display_daysymbol(oled2);
  }
  /* ------------------------------------------------- */
  /* Show Azimuth and sunrise/sunset to OLED1          */
  /* ------------------------------------------------- */
  snprintf(aziStr, sizeof(aziStr), "A%03d", (int)round((azimuth) * 10 / 10.0));
  oled1.setFont(u8g2_font_inr19_mr);
  oled1.drawStr(0,26, aziStr);
  oled1.setFont(u8g2_font_t0_17_mr);
  oled1.setCursor(0, 47);
  oled1.print(riseStr);
  oled1.setCursor(0, 63);
  oled1.print(setStr);
  /* ------------------------------------------------- */
  /* Show time on OLED2                                */
  /* ------------------------------------------------- */
  snprintf(dateStr, sizeof(dateStr), "20%d/%02d/%02d",
  rtc.year(),rtc.month(),rtc.day());
  snprintf(timeStr, sizeof(timeStr), "%02d:%02d:%02d",
  rtc.hour(),rtc.minute(),rtc.second());
  oled2.setFont(u8g2_font_t0_17_mr);
  oled2.setCursor(0, 47);
  oled2.print(dateStr);
  oled2.setCursor(0, 63);
  oled2.print(timeStr);

  /* ------------------------------------------------- */
  /* Aquire compass sensor data                        */
  /* ------------------------------------------------- */
  compass.read();
  
  /* ------------------------------------------------- */
  /* If the sensor board orientation is unaligned, set */
  /* compass.heading((LSM303::vector<int>){0,1,0}) for */
  /* pointing along the Y-axis for example. Remove if  */
  /* the X-axis is the point of reference on a LSM303D */
  /* ------------------------------------------------- */
  /* Because magnetic north != real north, we adjust:  */
  /* Calculate magnetic declination and convergence    */
  /* to determine true North from magnetic North       */ 
  /* https://www.ngdc.noaa.gov/geomag/WMM/soft.shtml   */
  /* ------------------------------------------------- */
  //heading = compass.heading((LSM303::vector<int>){0,-1,0}) + mdecl;
  heading = compass.heading() + mdecl;
  
  /* ------------------------------------------------- */
  /* print North heading to OLED2                      */
  /* ------------------------------------------------- */
  hdg = (int16_t)round((heading) * 10 / 10.0);
  if(hdg < 0) hdg = 360 + hdg;
  snprintf(dirStr, sizeof(dirStr), "H%03d", hdg);
  oled2.setFont(u8g2_font_inr19_mr);
  oled2.drawStr(0,26, dirStr);

  /* ------------------------------------------------- */
  /* Convert heading angle to LED range value (0..32)  */   
  /* ------------------------------------------------- */
  hled = (uint8_t)round((heading / 11.25) * 10 / 10.0);
  aled = (uint8_t)round((azimuth / 11.25) * 10 / 10.0);
  rled = (uint8_t)round((riseaz / 11.25) * 10 / 10.0);
  sled = (uint8_t)round((setaz / 11.25) * 10 / 10.0);
  /* ------------------------------------------------- */
  /* If 32 is returned, it should roll over to 0       */   
  /* ------------------------------------------------- */
  if(hled > 31) hled = 0;
  if(aled > 31) aled = 0;
  if(rled > 31) rled = 0;
  if(sled > 31) sled = 0;
  /* ------------------------------------------------- */
  /* Because LED-1 is 90 degrees offset, we compensate */
  /* ------------------------------------------------- */
  hled = hled + 24; if(hled > 31) hled = hled - 32;
  /* ------------------------------------------------- */
  /* Reverse counting to keep the LED aligned to North */
  /* ------------------------------------------------- */
  hled = 32 - hled; if(hled > 31) hled = 0;
  /* ------------------------------------------------- */
  /* Remaining LED follow heading                      */
  /* ------------------------------------------------- */
  aled = hled + aled; if(aled > 31) aled = aled - 32;
  rled = hled + rled; if(rled > 31) rled = rled - 32;
  sled = hled + sled; if(sled > 31) sled = sled - 32;

#ifdef DEBUG
   var2serial();
#endif 

  /* ------------------------------------------------- */
  /* motor1 target position follows azimuth LED value  */
  /* if 2nd dip switch enabled the motor. DIP2: LOW=ON */
  /* ------------------------------------------------- */
  if(dippos2 == LOW) {
    if(daylight) {
      if(m1move == false) {
        m1tpos = aled * 50;
        if(m1tpos != m1cpos) {
          motor1adjust(m1tpos, SLOW);
        }
      }
    }
    else {                /* nightfall, move motor-1 home */
      if(m1move == false) {
        if(m1tpos != 0) { /* are we already parked at D1? */
          m1tpos = 0;     /* set D1 home position until sunrise */
          motor1adjust(m1tpos, SLOW);
        }
      }
    }
  }

  /* ------------------------------------------------- */
  /* motor1 home when push button 1 is pressed  LOW=ON */
  /* ------------------------------------------------- */
  if(dippos2 == LOW) {
    if(m1move == false) {
      if(digitalRead(push1) == LOW) { motor1home(FAST); }
      if(digitalRead(push2) == LOW) { motor1led(FAST); }
    }
  }
  /* ------------------------------------------------- */
  /* Set heading LED                                   */
  /* ------------------------------------------------- */
  if (hled != oldhled) {
    if(oldhled < 16) mcp1.digitalWrite(oldhled, LOW);
    else if(oldhled < 32) mcp2.digitalWrite((oldhled-16), LOW);
    if(hled < 16) mcp1.digitalWrite(hled, HIGH);
    if(hled > 15) mcp2.digitalWrite((hled-16), HIGH);
    display_hdgled(oled2, oldhled, hled);
    oldhled = hled;
  }
  
  /* ------------------------------------------------- */
  /* Set azimuth LED                                   */
  /* ------------------------------------------------- */
  if (aled != oldaled) {
    if(oldaled < 16) mcp3.digitalWrite(oldaled, LOW);
    else if(oldaled < 32) mcp4.digitalWrite((oldaled-16), LOW);
    if(aled < 16) mcp3.digitalWrite(aled, HIGH);
    if(aled > 15) mcp4.digitalWrite((aled-16), HIGH);
    display_aziled(oled1, oldaled, aled);
    oldaled = aled;
  }

  /* ------------------------------------------------- */
  /* Set sunrise LED                                   */
  /* ------------------------------------------------- */
  if (rled != oldrled) {
    if(oldrled < 16) mcp1.digitalWrite(oldrled, LOW);
    else if(oldrled < 32) mcp2.digitalWrite((oldrled-16), LOW);
    if(rled < 16) mcp1.digitalWrite(rled, HIGH);
    if(rled > 15) mcp2.digitalWrite((rled-16), HIGH);
    oldrled = rled;
  }
  
  /* ------------------------------------------------- */
  /* Set sunset LED                                   */
  /* ------------------------------------------------- */
  if (sled != oldsled) {
    if(oldsled < 16) mcp1.digitalWrite(oldsled, LOW);
    else if(oldsled < 32) mcp2.digitalWrite((oldsled-16), LOW);
    if(sled < 16) mcp1.digitalWrite(sled, HIGH);
    if(sled > 15) mcp2.digitalWrite((sled-16), HIGH);
    oldsled = sled;
  }

  oled1.updateDisplay();
  oled2.updateDisplay();
  delay(50);
}

/* ------------------------------------------------- */
/* get solar postion record for current time.        */
/* ------------------------------------------------- */
void solar_position(char *file) {
  uint8_t linebuf[19];
  File bin = SD.open(file);
  while (bin.available()) {
    bin.read(linebuf, sizeof(linebuf));
    if(linebuf[0] == rtc.hour() && linebuf[1] == rtc.minute()) {
      memcpy(&azimuth, &linebuf[3], sizeof(double));
      memcpy(&zenith, &linebuf[11], sizeof(double));
      if(linebuf[2] == 1) daylight = 1;
      else daylight = 0;
      break;
    }
  }
  bin.close();
}
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

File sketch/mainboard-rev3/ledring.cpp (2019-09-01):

/* ---------------------------------------------------- *
 * Suntracker2  mainboard-rev3 ledring.c 2019-07 @FM4DD *
 *                                                      *
 * This file has the functions to control the dualcolor *
 * 32 LED ring on the Displayboard v2.0, which connects *
 * to the Suntracker2 Base-Board v1.7.                  *
 * ---------------------------------------------------- */
#include "ledring.h" // local module for the 32 LED ring

/* ---------------------------------------------------- */
/* 4x IO Expanders for a total of 64 I/O ports          */
/* ---------------------------------------------------- */
Adafruit_MCP23017 mcp1;
Adafruit_MCP23017 mcp2;
Adafruit_MCP23017 mcp3;
Adafruit_MCP23017 mcp4;

/* ---------------------------------------------------- */
/* led_enable() initializes the 4 GPIO port expanders   */
/* ---------------------------------------------------- */
void ledRing::enable() {
  mcp1.begin(0);     /* Enable the MCP23017 module 1 */
  mcp2.begin(1);     /* Enable the MCP23017 module 2 */
  mcp3.begin(2);     /* Enable the MCP23017 module 3 */
  mcp4.begin(3);     /* Enable the MCP23017 module 4 */
  /* Configure all MCP23017 ports in LED output mode */
  for(int i=0; i<16; i++) {
    mcp1.pinMode(i, OUTPUT);
    mcp2.pinMode(i, OUTPUT);
    mcp3.pinMode(i, OUTPUT);
    mcp4.pinMode(i, OUTPUT);
    mcp1.digitalWrite(i, LOW);
    mcp2.digitalWrite(i, LOW);
    mcp3.digitalWrite(i, LOW);
    mcp4.digitalWrite(i, LOW);
  }
}

/* ---------------------------------------------------- */
/* all_ledoff() turns off 32 LED, regardless of state   */
/* ---------------------------------------------------- */
void ledRing::all_ledoff() {
  mcp1.writeGPIOAB(0x00); /* expander1 all green LED off */
  mcp2.writeGPIOAB(0x00); /* expander2 all green LED off */
  mcp3.writeGPIOAB(0x00); /* expander3 all red LED off   */
  mcp4.writeGPIOAB(0x00); /* expander3 all red LED off   */
}

/* ---------------------------------------------------- */
/* led_lightcheck() LED on/off tests for all 4 units:   */
/* Blink all ports. 0xFFFF lights both GPIOA and GPIOB  */
/* Setting 0xFF only lights A, 0x00FF lights up only B  */
/* ---------------------------------------------------- */
void ledRing::lightcheck() {
  mcp1.writeGPIOAB(0xFFFF); /* expander1 all green LED on  */
  delay(500);
  mcp1.writeGPIOAB(0x00);   /* expander1 all green LED off */
  mcp2.writeGPIOAB(0xFFFF); /* expander2 all green LED on  */
  mcp3.writeGPIOAB(0xFFFF); /* expander3 all red LED on    */
  delay(500);
  mcp2.writeGPIOAB(0x00);   /* expander2 all green LED off */
  mcp3.writeGPIOAB(0x00);   /* expander3 all red LED off   */
  mcp4.writeGPIOAB(0xFFFF); /* expander4 all red LED on    */
  delay(500);
  mcp4.writeGPIOAB(0x00);   /* expander4 all red LED off   */
}

// Below two functions are commented out because I have
// the same functions in the main file with additional
// code for OLED status display.
/* ----------------------------------------------------- */
/* Single LED walkthrough - Red: mcp1,2, port A,B        */
/* Runs a single red LED light around the circle.        */
/* ----------------------------------------------------- */
//void stepled_red(int millisec) {
//  all_ledoff();                          /* reset LEDs   */
//  for(int i=0; i<16; i++) {              /* IO expander1 */
//    mcp1.digitalWrite(i, HIGH);          /* next LED on  */
//    if(i>0) mcp1.digitalWrite(i-1, LOW); /* prev LED off */
//    delay(millisec);                     /* speed in ms  */
//  }
//  mcp1.digitalWrite(15, LOW);             /* last LED off */
//  for(int i=0; i<16; i++) {               /* IO expander2 */
//    mcp2.digitalWrite(i, HIGH);           /* next LED on  */
//    if(i>0) mcp2.digitalWrite(i-1, LOW);  /* prev LED off */
//    delay(millisec);                      /* speed in ms  */
//  }
//  mcp2.digitalWrite(15, LOW);             /* last LED off */
//}

/* ------------------------------------------------------ */
/* Single LED walkthrough - Green: mcp3,4, port C,D       */
/* Runs a single green LED light around the circle.       */
/* ------------------------------------------------------ */
//void stepled_green(int millisec) {
//  all_ledoff();                           /* reset LEDs   */
// for(int i=0; i<16; i++) {               /* IO expander3 */
//    mcp3.digitalWrite(i, HIGH);           /* next LED on  */
//    if(i>0) mcp3.digitalWrite(i-1, LOW);  /* prev LED off */
//    delay(millisec);                      /* speed in ms  */
//  }
//  mcp3.digitalWrite(15, LOW);
//  for(int i=0; i<16; i++) {               /* IO expander4 */
//    mcp4.digitalWrite(i, HIGH);           /* next LED on  */
//    if(i>0) mcp4.digitalWrite(i-1, LOW);  /* prev LED off */
//    delay(millisec);                      /* speed in ms  */
//  }
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

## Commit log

2019-07-20 repo setup
    [20190601 stepper motor footprint.dxf, 20190620 Suntracker2 Bottom v1.0.dxf, 20190620 Suntracker2 Top v1.0.dxf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]
2019-07-20 fix bom column
    [mainboard-v1.7-bom.csv]
2019-07-20 fix bom csv
    [mainboard-v1.7-bom.csv]
2019-07-28 Arduino sketch module creation
2019-08-04 add displayboard gerber
2019-08-04 mainboard gerber fix
2019-08-10 BOM update, add displayboard schema
    [displayboard-v2.0-bom.csv, mainboard-v1.7-bom.csv, mainboard-v1.8-bom.csv]
2019-08-14 Add OLEDs to BOM
    [displayboard-v2.0-bom.csv]
2019-09-01 add LED displaymode 2
